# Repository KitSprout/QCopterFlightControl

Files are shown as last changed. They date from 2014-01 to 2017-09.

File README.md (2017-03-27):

QCopterFC
========





QCopterFC 是一個基於 STM32F4 的飛行控制器，主要用來實現濾波、平衡、控制等演算法的平台。集成微控制器 9 DOF 慣性測量元件以及氣壓計，目前有 QCopterFC 與 QCopterFCs 兩種版本，前者使用芯片效能較高、功能多、硬體完善，後者功能較為簡潔，以擴充方式實現不同需求，靈活度高。目前開發著重於 QCopterFCs，想了解 QCopterFC 的可以進入該分支 [branche](https://github.com/KitSprout/QCopterFlightControl/tree/QCopterFC)

Hardware
========
* 控制器　 : [STM32F411CE](http://www.st.com/en/microcontrollers/stm32f411ce.html) 48Pin 100MHz DSP FPU
* 感測器　 : [MPU9250](https://www.invensense.com/products/motion-tracking/9-axis/mpu-9250/) + [LPS22HB](http://www.st.com/en/mems-and-sensors/lps22hb.html)
* PCB 尺寸 : 26 * 26mm ( Screws M3: 20 * 20mm )
* 設計軟體 [Altium Designer 17](http://www.altium.com/en/products/altium-designer) ( PcbLib use AD [PcbLib v2.16](https://github.com/KitSprout/AltiumDesigner_PcbLibrary/releases/tag/v2.16) )

View
========


<br />
[more photo](https://goo.gl/photos/LVRgoCt4GyYr4dVZ8)...

Config
========


Schematic
========


Get it
========
Ruten Shop

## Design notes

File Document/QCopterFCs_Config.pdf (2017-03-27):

PORT | AF0 SYS | AF1 TIM1 TIM2 | AF2 TIM3 TIM4 TIM5 | AF3 TIM9 TIM10 TIM11 | AF4 I2C1 I2C2 I2C3 | AF5 SPI1 SPI2 SPI4 | AF6 SPI3 SPI4 SPI5 | AF7 SPI3 USART1 USART2 | AF8 USART6 | AF9 I2C2 I2C3 | AF10 OTG_FS | AF12 SDIO | ADC | 配置

PA

PB

PC

0 | CH1 / ETR | CH1 | CTS | ADC1_IN0 | O | EA0
1 | CH2 | CH2 | MOSI | RTS | ADC1_IN1 | O | EA1
2 | CH3 | CH3 | CH1 | TX | ADC1_IN2 | O | EA2
3 | CH4 | CH4 | CH2 | RX | ADC1_IN3 | O | EA3
4 | NSS | NSS | CK | ADC1_IN4 | O | IMU_CSM
5 | CH1 / ETR | SCK | ADC1_IN5 | O | IMU_SCK
6 | BKIN | CH1 | MISO | CMD | ADC1_IN6 | O | IMU_SDO
7 | CH1N | CH2 | MOSI | ADC1_IN7 | O | IMU_SDI
8 | MCO1 | CH1 | SCL | CK | SOF | D1 | O | EA8
9 | CH2 | SMBA | TX | VBUS | D2 | O | EA9
10 | CH3 | MOSI | RX | ID | O | EA10
11 | CH4 | MISO | CTS | TX | DM | X | USB_DM
12 | ETR | MISO | RTS | RX | DP | X | USB_DP
13 | SDIO | O | SWDIO
14 | SCLK | O | SWCLK
15 | JTDI | CH1 / ETR | NSS | NSS | TX | O | EA15
0 | CH2N | CH3 | SCK | ADC1_IN8 | O | EB0
1 | CH3N | CH4 | NSS | ADC1_IN9 | O | EB1
2 | BOOT | O | KEY
3 | JTDO | CH2 | SCK | SCK | RX | SDA | O | EB3
4 | JTRST | CH1 | MISO | MISO | SDA | D0 | O | EB4
5 | CH2 | SMBA | MOSI | MOSI | D3 | O | EB5
6 | CH1 | SCL | TX | O | EB6
7 | CH2 | SDA | RX | D0 | O | EB7
8 | CH3 | CH1 | SCL | MOSI | SDA | D4 | O | EB8
9 | CH4 | CH1 | SDA | NSS | SDA | D5 | O | EB9
10 | CH3 | SCL | SCK | D7 | O | IMU_CSB
11 | CH4 | X
12 | BKIN | SMBA | NSS | NSS | SCK | O | EP12
13 | CH1N | SCK | SCK | O | EB13
14 | CH2N | MISO | D6 | O | EB14
15 | RTC | CH3N | MOSI | CK | O | EB15
13 | O | LED_R
14 | O | LED_G
15 | O | LED_B

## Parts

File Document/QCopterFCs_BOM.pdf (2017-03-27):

Comment | Description | Designator | Footprint | LibRef | Quantity | Value
Cap_0603 | Capacitor | C1, C2, C3, C4 | CAP_0603 | Cap_0603 | 4 | 1u, 0.1u, 0.1u, 22n
Cap_0402 | Capacitor | C5, C6, C7, C8, C9, C11, C12, C13, C14, C15, C16 | CAP_0402 | Cap_0402 | 11 | 0.1u, 0.1u, 0.1u, 0.1u, 0.1u, 10p, 10p, 10n, 0.1u, 0.1u, 0.1u
Cap_Tan_0805 | Capacitor | C10 | CAP_TAN_P0805 | Cap_Tan_0805 | 1 | 2.2u
LED_0603 | LED | D1 | LED_0603_YELLOW | LED_0603 | 1
LED_1616_RGB | LED | D2 | LED_1616_RGB | LED_1616_RGB | 1
HDR2x10_1.27 | Header | HDR1, HDR2 | HDR2X10_1.27_18 0S | HDR2x10_1.27 | 2
ButtonTACT | Button | KEY | ButtonTACT_3.5*3. 55_90 | ButtonTACT | 1
Res_0402 | Resistor | R1, R2, R3, R5, R6, R7, R8, R9, R10, R11, R12 | RES_0402 | Res_0402 | 11 | 1.5K, 22R, 22R, 10K, 10K, 680R, 1K, 220R, 10K, 4.7K, 4.7K
Res_0603 | Resistor | R4 | RES_0603 | Res_0603 | 1 | 1K
RT9193 | Power | U1 | SOT23-5 | RT9193 | 1
STM32F411C | MCU | U2 | QFN_P0.5_48 | STM32F4x1C | 1
MPU925x | Sensor Motion | U3 | QFN_P0.4_24 | MPU925x | 1
LPS22HB | Sensor Pressure | U4 | HCLGA-2x2_10 | LPS22HB | 1
USB_Micro | USB | USB | USB_Micro-AB | USB_Micro | 1
XTAL_2520_4P | Crystal Oscillator | XT | XT_2520_4 | XTAL_2520_4P | 1 | 16MHz

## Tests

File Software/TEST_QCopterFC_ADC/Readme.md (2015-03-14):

QCopterFC ADC Example
========
* Author  : [Hom](about.me/Hom)
* Update  : 2014/05/06

Description
========
QCopterFC ADC 的範例程式，連續讀取 ADC_I 和 ADC_V 資料，同時 LED_G 會一直閃爍。

Hardware
========
* LED  
PC13 - LED_B  
PC14 - LED_G  
PC15 - LED_R  

* KEY  
PB2  - KEY  

* ADC  
PC4  - ADC_I  
PC5  - ADC_V  

* UART  
PB6 - UART Tx  
PB7 - UART Rx  
> UARTx = USART1  
> BaudRate = 115200  
> ByteSize = 8  
> StopBits = 1  
> Parity = 'N'  
> HardwareFlowControl = None

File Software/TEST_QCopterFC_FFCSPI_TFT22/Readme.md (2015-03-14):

QCopterFC FFCSPI-TFT2.2 Example
========
* Author  : [Hom](http://about.me/home)
* Update  : 2014/06/10

Description
========
QCopterFC FFCSPI-TFT2.2 的範例程式，透過 FFCSPI 讀寫 2.2 吋螢幕，並顯示彩條。

Hardware
========
* LED  
PC13 - LED_B  
PC14 - LED_G  
PC15 - LED_R  

* KEY  
PB2  - KEY  

* FFCSPI - TFT2.2  
PA4 - TFT22_CST  
PA5 - TFT22_SCK  
PA6 - TFT22_SDO  
PA7 - TFT22_SDI  
PC0 - TFT22_RST  
PC1 - TFT22_DC  
> SPIx = SPI1  
> Dir = 2Lines_FullDuplex  
> Mode = Slave  
> CPOL = High  
> CPHA = 2Edge  
> FirstBit = MSB  
> DataSize = 8 bits  
> BaudRate = Prescaler_2

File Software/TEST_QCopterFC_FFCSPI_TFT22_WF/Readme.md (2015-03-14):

QCopterFC FFCSPI-TFT2.2_WaveForm Example
========
* Author  : [Hom](http://about.me/home)
* Update  : 2014/06/10

Description
========
QCopterFC TFT2.2_WaveForm 的範例程式，透過 FFCSPI 讀寫 2.2 吋螢幕，計算三角函數並將波形顯示出來。

Hardware
========
* LED  
PC13 - LED_B  
PC14 - LED_G  
PC15 - LED_R  

* KEY  
PB2  - KEY  

* FFCSPI - TFT2.2  
PA4 - TFT22_CST  
PA5 - TFT22_SCK  
PA6 - TFT22_SDO  
PA7 - TFT22_SDI  
PC0 - TFT22_RST  
PC1 - TFT22_DC  
> SPIx = SPI1  
> Dir = 2Lines_FullDuplex  
> Mode = Slave  
> CPOL = High  
> CPHA = 2Edge  
> FirstBit = MSB  
> DataSize = 8 bits  
> BaudRate = Prescaler_2

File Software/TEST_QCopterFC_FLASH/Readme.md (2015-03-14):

QCopterFC FLASH Example
========
* Author  : [Hom](http://about.me/Hom)
* Update  : 2014/07/10

Description
========
QCopterFC FLASH 的範例程式，分成三種資料型態 U8 U16 U32 寫入，並讀出來比較是否正確，若正確則 LED 會依序發亮，最後一起閃爍。

Hardware
========
* LED  
PC13 - LED_B  
PC14 - LED_G  
PC15 - LED_R

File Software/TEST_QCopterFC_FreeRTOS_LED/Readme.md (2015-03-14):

QCopterFC LED Example
========
* Author  : [Hom](about.me/Hom)
* Update  : 2014/07/01

Description
========
QCopterFC 運行 FreeRTOS 的 LED 範例程式，LED_R 閃爍週期 1000 ms、LED_G 閃爍週期 500 ms、LED_B 閃爍週期 250 ms。  

Hardware
========
* LED  
PC13 - LED_B  
PC14 - LED_G  
PC15 - LED_R

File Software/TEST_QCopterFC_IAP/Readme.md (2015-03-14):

QCopterFC IAP Example
========
* Author  : [Hom](http://about.me/Hom)
* Update  : 2014/07/08

Description
========
QCopterFC IAP 的範例程式，按著 KEY 開機，將進入 BOOT 模式，此時會從 UART 接收 .bin 檔案，寫入至 APP FLASH 區域並執行，若開機未按下 KEY 則直接進入 APP 模式，執行最後更新的 APP 程式。  

Hardware
========
* LED  
PC13 - LED_B  
PC14 - LED_G  
PC15 - LED_R  

* KEY  
PB2  - KEY  

* UART  
PB6 - UART Tx  
PB7 - UART Rx  
> UARTx = USART1  
> BaudRate = 115200  
> ByteSize = 8  
> StopBits = 1  
> Parity = 'N'  
> HardwareFlowControl = None

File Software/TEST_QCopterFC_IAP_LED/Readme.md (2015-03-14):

QCopterFC IAP-LED Example
========
* Author  : [Hom](http://about.me/Hom)
* Update  : 2014/07/08

Description
========
QCopterFC IAP 的 LED 和 KEY 範例程式，啟動時 LED 會依序閃爍 ( R → G → B )，當按下按鍵 KEY 時，LED 則會同時閃爍，放開按鍵又會依序閃爍。  
 > 詳細參考 TEST_QCopterFC_LED

Hardware
========
* LED  
PC13 - LED_B  
PC14 - LED_G  
PC15 - LED_R  

* KEY  
PB2  - KEY

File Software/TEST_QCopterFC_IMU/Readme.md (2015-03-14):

QCopterFC IMU Example
========
* Author  : [Hom](http://about.me/Hom)
* Update  : 2014/06/10

Description
========
QCopterFC IMU 的範例程式，以 500Hz 讀取感測器，並透過 RS232 將資料傳送至 PC 端的 VisualScope 做顯示。

Hardware
========
* LED  
PC13 - LED_B  
PC14 - LED_G  
PC15 - LED_R  

* KEY  
PB2  - KEY  

* UART  
PB10 - UART Tx  
PB11 - UART Rx  
> UARTx = USART3  
> BaudRate = 9600  
> ByteSize = 8  
> StopBits = 1  
> Parity = 'N'  
> HardwareFlowControl = None  

* SPI  
PB13 - SPI_SCK  
PB14 - SPI_SDO  
PB15 - SPI_SDI  
PC2  - SPI_CSM  
> SPIx = SPI2  
> Dir = 2Lines_FullDuplex  
> Mode = Slave  
> CPOL = High  
> CPHA = 2Edge  
> FirstBit = MSB  
> DataSize = 8 bits  
> BaudRate = Prescaler_256

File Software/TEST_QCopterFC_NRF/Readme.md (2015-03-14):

QCopterFC NRF Example
========
* Author  : [Hom](about.me/Hom)
* Update  : 2014/05/12

Description
========
QCopterFC NRF 的範例程式，透過定義 NRF_MODE 來決定先發射還是先接收，
先發送的為 FTLR，先接收的為 FRLT，FTLR 板子會先傳送資料至 FRLT，
FRLT 收到後會直接回傳，並將資料透過 RS232 在 PC 端顯示，同時閃爍 LED_G & LED_B，
FTLR 則會將接收到的資料加上資料地址的數值發送至 FRLT，不斷循環，並閃爍 LED_R & LED_B。

Hardware
========
* LED  
PC13 - LED_B  
PC14 - LED_G  
PC15 - LED_R  

* KEY  
PB2  - KEY  

* UART  
PB6 - UART Tx  
PB7 - UART Rx  
> UARTx = USART1  
> BaudRate = 115200  
> ByteSize = 8  
> StopBits = 1  
> Parity = 'N'  
> HardwareFlowControl = None  

* NRF  
PA8  - CE  
PA15 - CSN  
PB3  - SCK  
PB4  - MISO  
PB5  - MOSI  
PB12 - IRQ  
> SPIx　　 = SPI3  
> Dir　　　= 2Lines_FullDuplex  
> Mode　　 = Master  
> CPOL　　 = Low  
> CPHA　　 = 1Edge  
> FirstBit = MSB  
> DataSize = 8 bits  
> BaudRate = Prescaler_4

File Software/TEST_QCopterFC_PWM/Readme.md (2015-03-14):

QCopterFC PWM Example
========
* Author  : [Hom](about.me/Hom)
* Update  : 2014/05/06

Description
========
QCopterFC PWM 的範例程式，按下按鍵 KEY 時，會改變 PWM 的 Duty Cycle，LED 同時會閃爍。

Hardware
========
* LED  
PC13 - LED_B  
PC14 - LED_G  
PC15 - LED_R  

* KEY  
PB2  - KEY  

* PWM  
PA0  - TIM2 CH1 - PWM1  
PA1  - TIM2 CH2 - PWM2  
PA2  - TIM2 CH3 - PWM3  
PA3  - TIM2 CH4 - PWM6  
PB0  - TIM3 CH3 - PWM5 
PB1  - TIM3 CH4 - PWM4  
PB8  - TIM4 CH3 - PWM10  
PB9  - TIM4 CH4 - PWM11  
PC6  - TIM3 CH1 - PWM8  
PC7  - TIM3 CH2 - PWM7

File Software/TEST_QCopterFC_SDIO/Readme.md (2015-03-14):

QCopterFC SDIO Example
========
* Author  : [Hom](about.me/Hom)
* Update  : 2014/05/09

Description
========
QCopterFC SDIO 搭配 FatFs 的範例程式，從一開始的 SD 卡初始化、SD 卡資訊、讀取資料夾目錄、寫檔案、讀檔案的整體測試。

Hardware
========
* LED  
PC13 - LED_B  
PC14 - LED_G  
PC15 - LED_R  

* UART  
PB6 - UART Tx  
PB7 - UART Rx  
> UARTx = USART1  
> BaudRate = 115200  
> ByteSize = 8  
> StopBits = 1  
> Parity = 'N'  
> HardwareFlowControl = None  

* SDIO  
PD8  - SDIO D0  
PD9  - SDIO D1  
PD10 - SDIO D2  
PD11 - SDIO D3  
PD12 - SDIO CK  
PD2  - SDIO CMD

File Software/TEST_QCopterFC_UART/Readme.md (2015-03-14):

QCopterFC UART Example
========
* Author  : [Hom](http://about.me/Hom)
* Update  : 2014/07/10

Description
========
QCopterFC UART 的範例程式，
USE_RS232：將鍵盤輸入的資料顯示在 Putty 上，同時綠色 LED 也會翻轉，
USE_VISUALSCOPE：將變數 i 透過 RS232 傳輸至電腦端，每傳一次 i 值就會加 1000，加到 32767 會從 -32768 重新開始再加，同時綠色 LED 也會閃爍。

Hardware
========
* LED  
PC13 - LED_B  
PC14 - LED_G  
PC15 - LED_R  

* UART  
PB6 - UART Tx  
PB7 - UART Rx  
> UARTx = USART1  
> BaudRate = 9600  
> ByteSize = 8  
> StopBits = 1  
> Parity = 'N'  
> HardwareFlowControl = None

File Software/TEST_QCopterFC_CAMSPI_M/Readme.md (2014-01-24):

QCopterFC CamSPI Master Example
========
* Author : [Hom](https://github.com/Hom19910422)
* Update : 2014/01/24

Description
========
QCopterFC CamSPI Master 的範例程式，當按下按鍵 KEY 時，CamSPI 會送出指令，並且接收回應，若正確 LED 則會發亮，最後會一起閃爍。  

Hardware
========
* LED  
PC13 - LED_B  
PC14 - LED_G  
PC15 - LED_R  

* KEY  
PB2  - KEY  

* CamSPI  
PA15 - CamSPI_CS  
PB3  - CamSPI_SCK  
PB4  - CamSPI_MISO  
PB5  - CamSPI_MOSI  
> SPIx = SPI3  
> Dir = 2Lines_FullDuplex  
> Mode = Master  
> CPOL = Low  
> CPHA = 1Edge  
> FirstBit = MSB  
> DataSize = 8 bits  
> BaudRate = Prescaler_256

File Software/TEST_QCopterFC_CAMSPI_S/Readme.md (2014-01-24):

QCopterFC CamSPI Slave Example
========
* Author : [Hom](https://github.com/Hom19910422)
* Update : 2014/01/24

Description
========
QCopterFC CamSPI Slave 的範例程式，接收到指令會回傳對應資料。  

Hardware
========
* LED  
PC13 - LED_B  
PC14 - LED_G  
PC15 - LED_R  

* CamSPI  
PA15 - CamSPI_CS  
PB3  - CamSPI_SCK  
PB4  - CamSPI_MISO  
PB5  - CamSPI_MOSI  
> SPIx = SPI3  
> Dir = 2Lines_FullDuplex  
> Mode = Slave  
> CPOL = Low  
> CPHA = 1Edge  
> FirstBit = MSB  
> DataSize = 8 bits  
> BaudRate = Prescaler_256

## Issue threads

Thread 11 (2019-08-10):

關於MPU9250的加速度計問題

smallchicken0204, 2019-08-10:
您好，我是台北大學資工系的研究生，目前做的研究是將IMU放置在手腕上追蹤手部軌跡，而遇到的問題是，當加速度計從運動狀態急停的時候，似乎會出現與運動方向相反的加速度，導致軌跡會出現到達目標位置時(15CM處)，瞬間往後倒退3~5CM(12CM處)，想詢問您有沒有遇過相關的問題?

brennenhuang, 2019-08-10:
請問是real time還是事後分析呢？

smallchicken0204 <notifications@github.com>於 2019年8月10日 週六，下午5:02寫道：

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

smallchicken0204, 2019-08-10:
real time的，我是設計成每收集20筆加速度資料，進行一次計算。

brennenhuang, 2019-08-10:
如果軌跡在動時有明確的起始，那可以用零速補償，如果是一直持續的動態一定會有積分飄移，然後記得用濾波器濾雜訊

smallchicken0204 <notifications@github.com>於 2019年8月10日 週六，下午8:35寫道：

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

smallchicken0204, 2019-08-10:
瞭解，目前有使用簡易的零速補償，我先嘗試去改良一下零速補償這塊看看，感謝您的回答。

brennenhuang, 2019-08-11:
加油keep going

smallchicken0204 <notifications@github.com>於 2019年8月10日 週六，下午10:12寫道：

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

smallchicken0204, 2019-10-03:
您好，我想再跟您請教一下MPU9250的問題，目前我打算驗證位移距離，所以做了一個軌道平台(如附圖一)，這平台是讓IMU單純沿著x軸來回滑動且軌道算是光滑不會震動，但是發現row data裡面的Z軸加速度會出現過大的振幅，所以我做了一個測試是在軌道滑動數次，再用手持IMU在空中移動數次，得到row data(如附圖二)Y軸是加速度(單位:g)X軸為樣本數，左邊紅色框框是在軌道上滑動得到的數值，右邊紅色框框則是空中滑動的，因為差異其實蠻大的，我不太能確定是否全為摩擦震動導致，想詢問您有沒有遇過相關的情況?
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

Closed 2019-10-08.

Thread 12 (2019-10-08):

MPU9250加速度Z軸的問題

smallchicken0204, 2019-10-08:
您好，我想跟您請教一下MPU9250的問題，目前我打算驗證位移距離，所以做了一個軌道平台(如附圖一)，這平台是讓IMU單純沿著x軸來回滑動，而且軌道算是光滑不會震動，但是發現row data裡面的Z軸加速度會出現過大的振幅，所以我做了一個測試是在軌道滑動數次，再用手持IMU在空中移動數次，得到row data(如附圖二)Y軸是加速度(單位:g)X軸為樣本數，左邊紅色框框是在軌道上滑動得到的數值，右邊紅色框框則是空中滑動的，因為差異其實蠻大的，我不太能確定是否全為摩擦震動導致，想詢問您有沒有遇過相關的情況?
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

brennenhuang, 2019-10-09:
看起來Z軸呈現的確實怪,你要不要把他的Z軸跟X軸或Y軸對調,重複做一樣的實驗,看會不會重現此問題,讓x或y軸朝上,祝你一切順利

On Tue, Oct 8, 2019 at 4:41 PM smallchicken0204 <notifications@github.com>
wrote:

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

smallchicken0204, 2019-10-10:
對調Y軸跟Z軸後，意外發現問題所在了，謝謝您的建議~

brennenhuang, 2019-10-10:
讚喔，之後有問題也可以用賴問，研究的問題通常都不太能等，我的賴：jimpaul15，如果有要加可以說一聲，我剛好也在台北工作，加油嘍，對了也可以用email問，只是通常可能不會天天看email

smallchicken0204 <notifications@github.com>於 2019年10月10日 週四，下午3:42寫道：

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

smallchicken0204, 2019-10-11:
好的，那我加一下您的Line。

Closed 2019-10-10.

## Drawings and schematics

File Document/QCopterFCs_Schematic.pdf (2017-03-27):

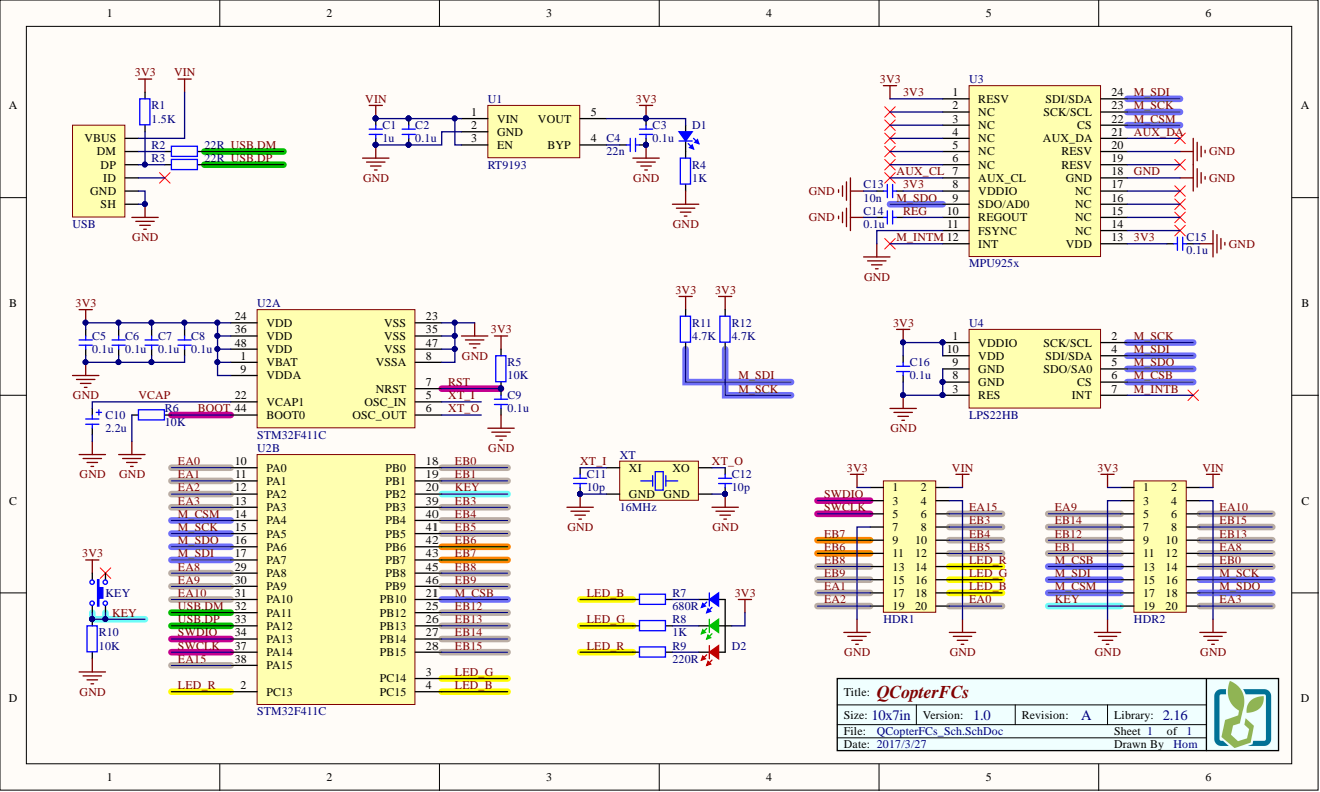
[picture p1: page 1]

3 6 | 3 5
4 8 | 4 7

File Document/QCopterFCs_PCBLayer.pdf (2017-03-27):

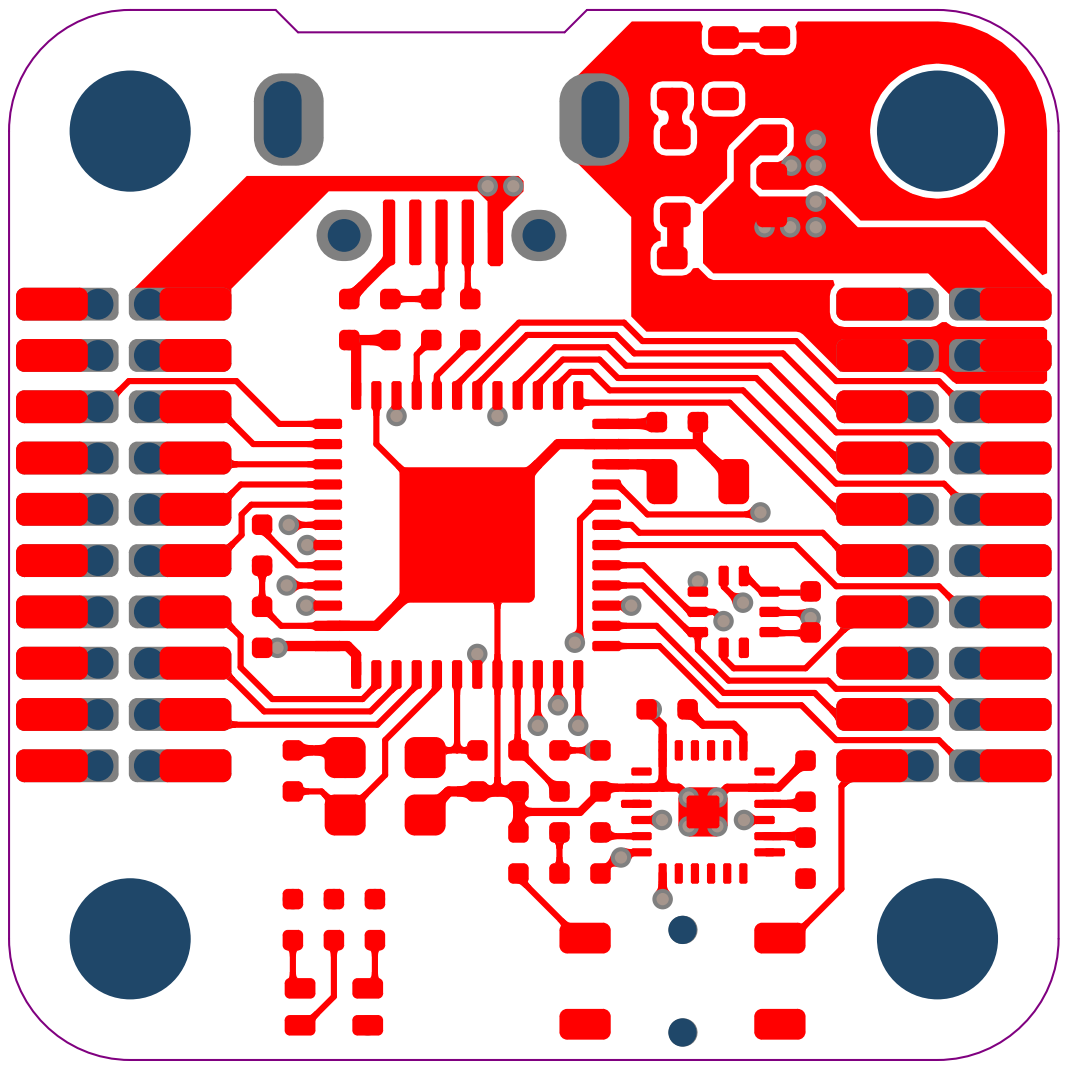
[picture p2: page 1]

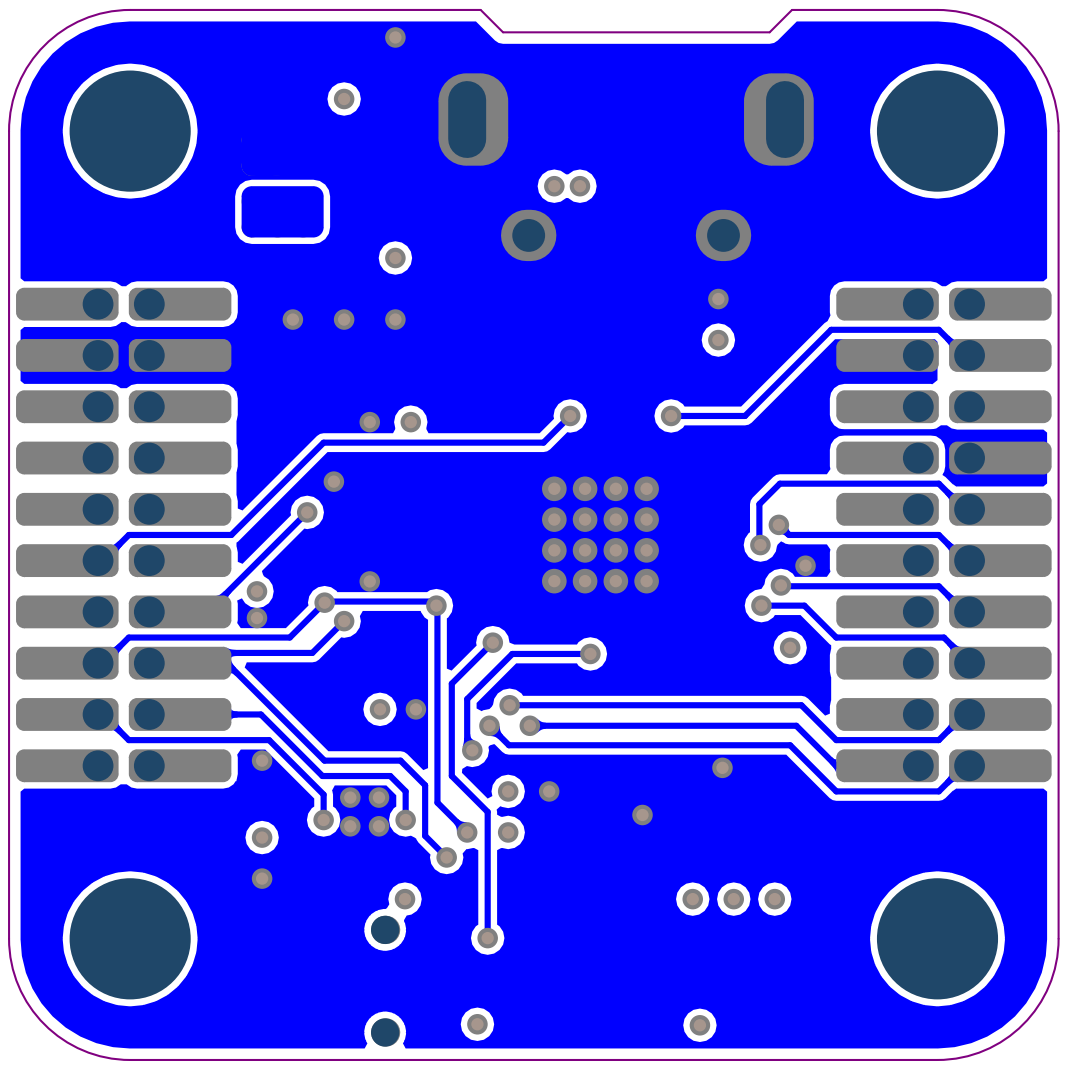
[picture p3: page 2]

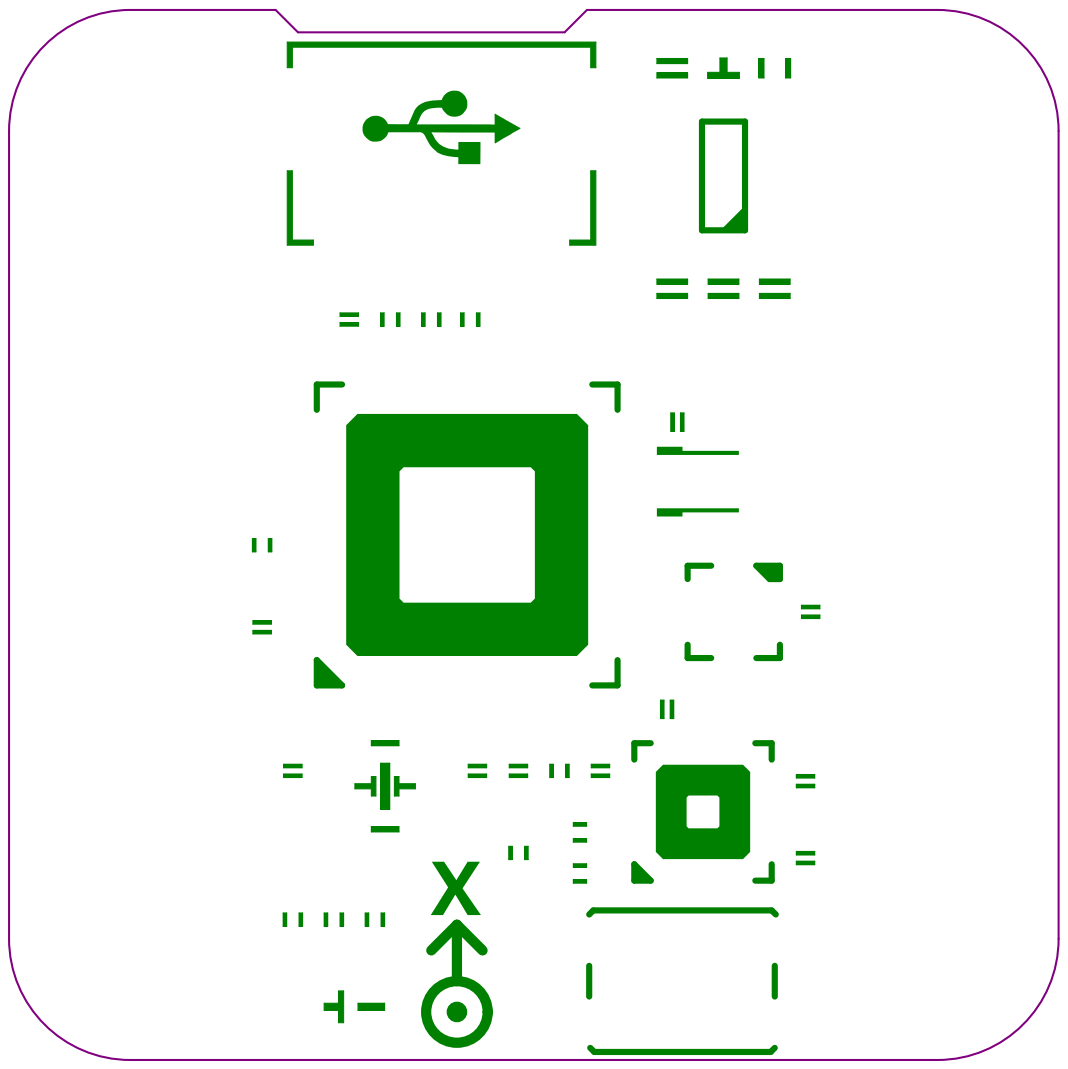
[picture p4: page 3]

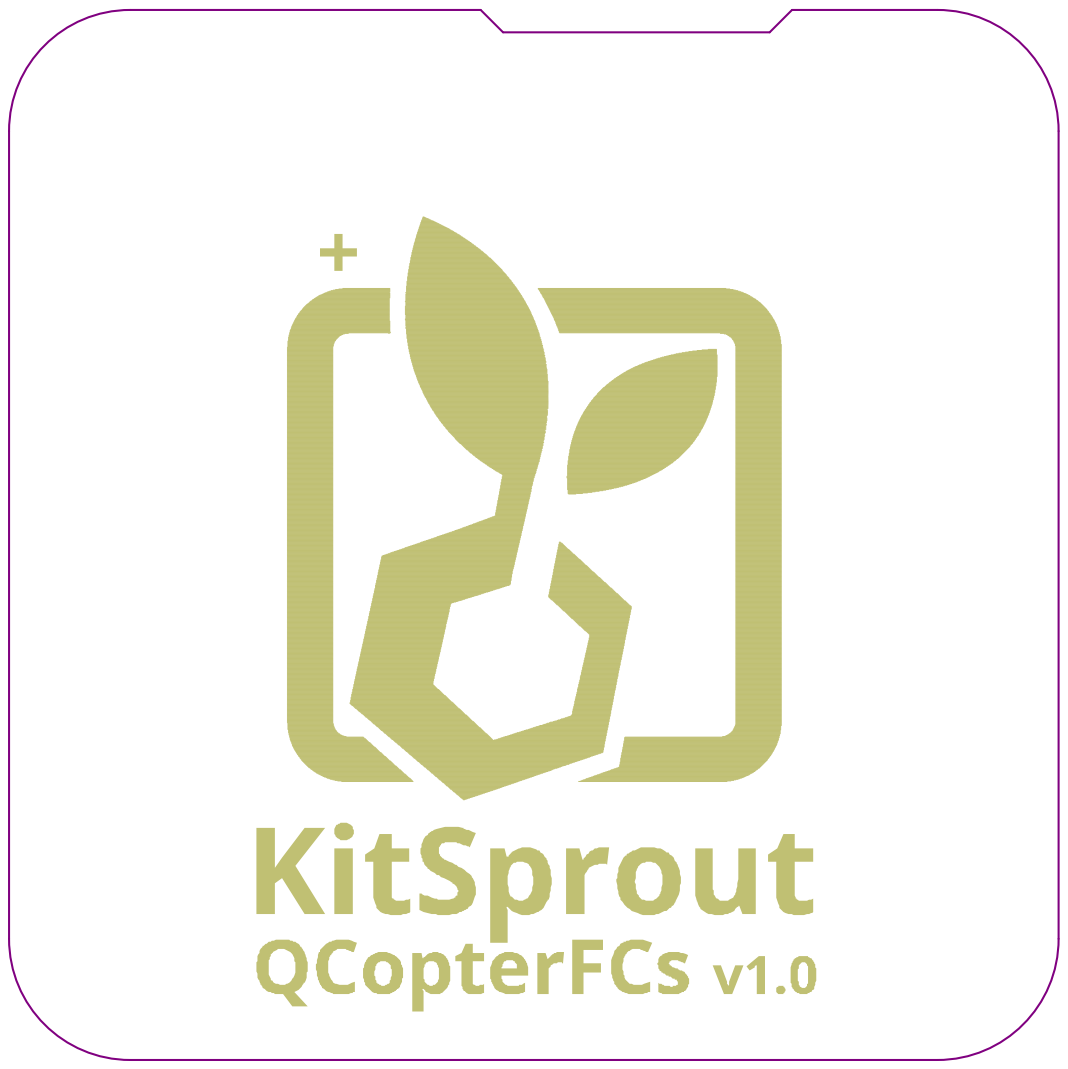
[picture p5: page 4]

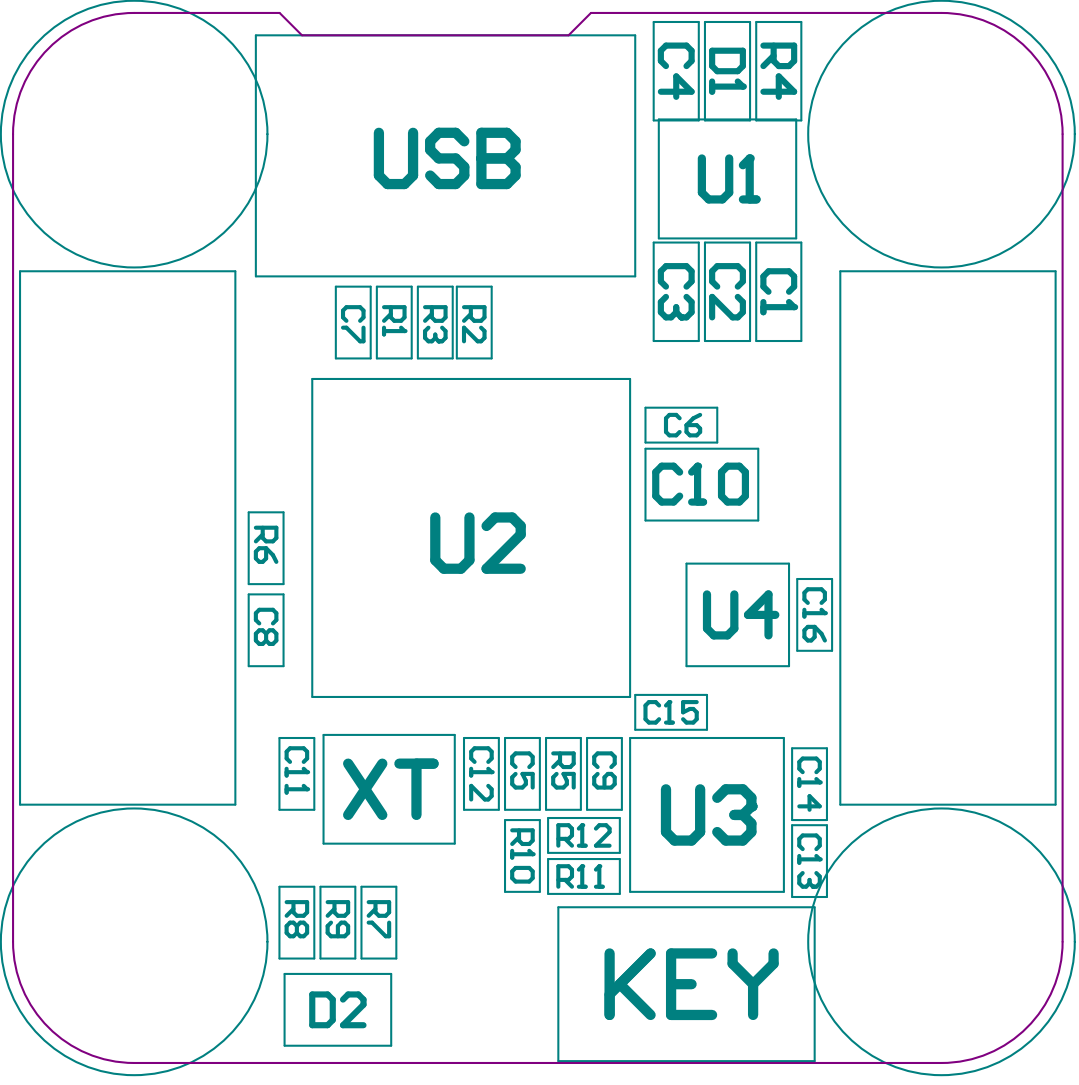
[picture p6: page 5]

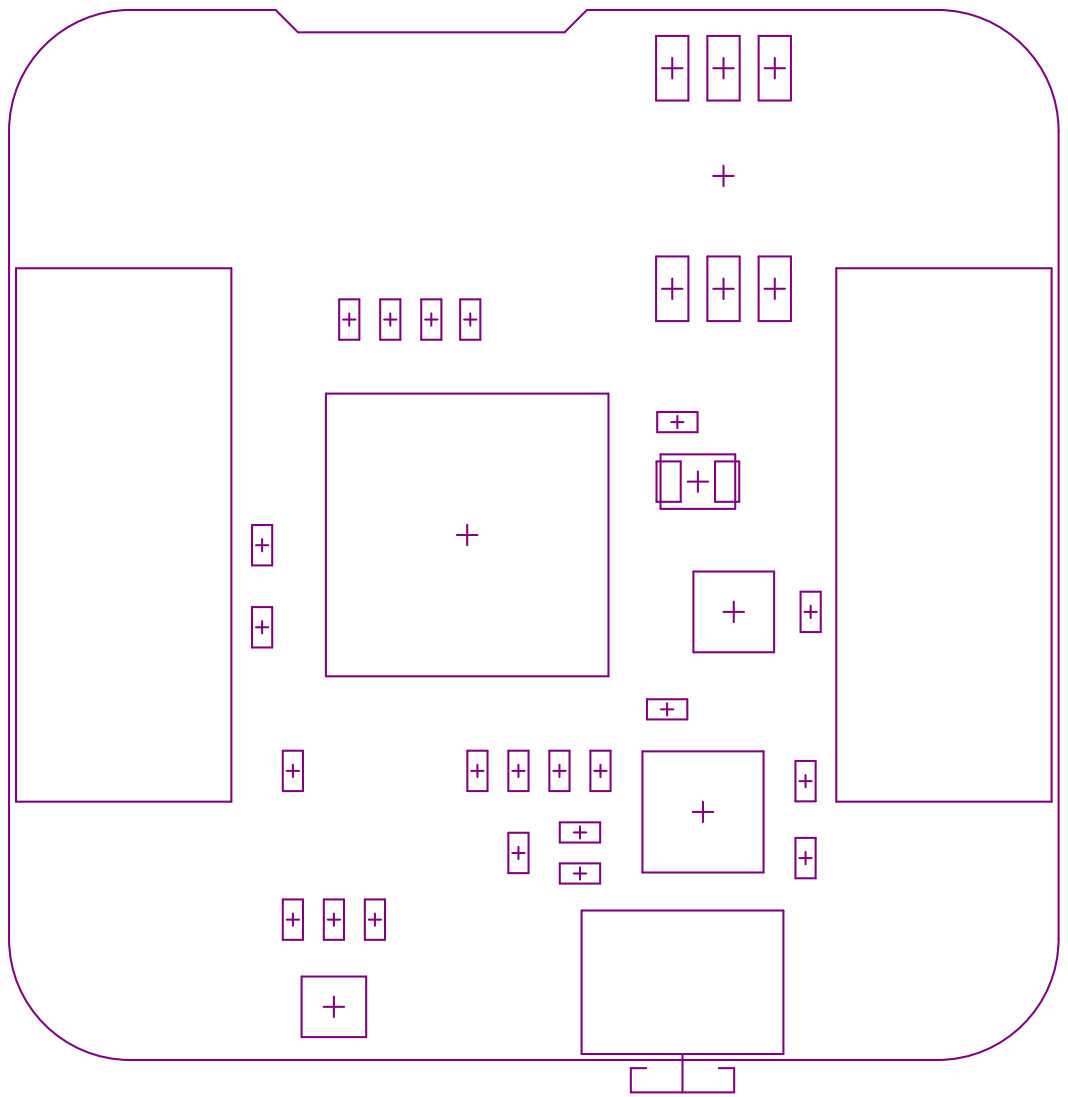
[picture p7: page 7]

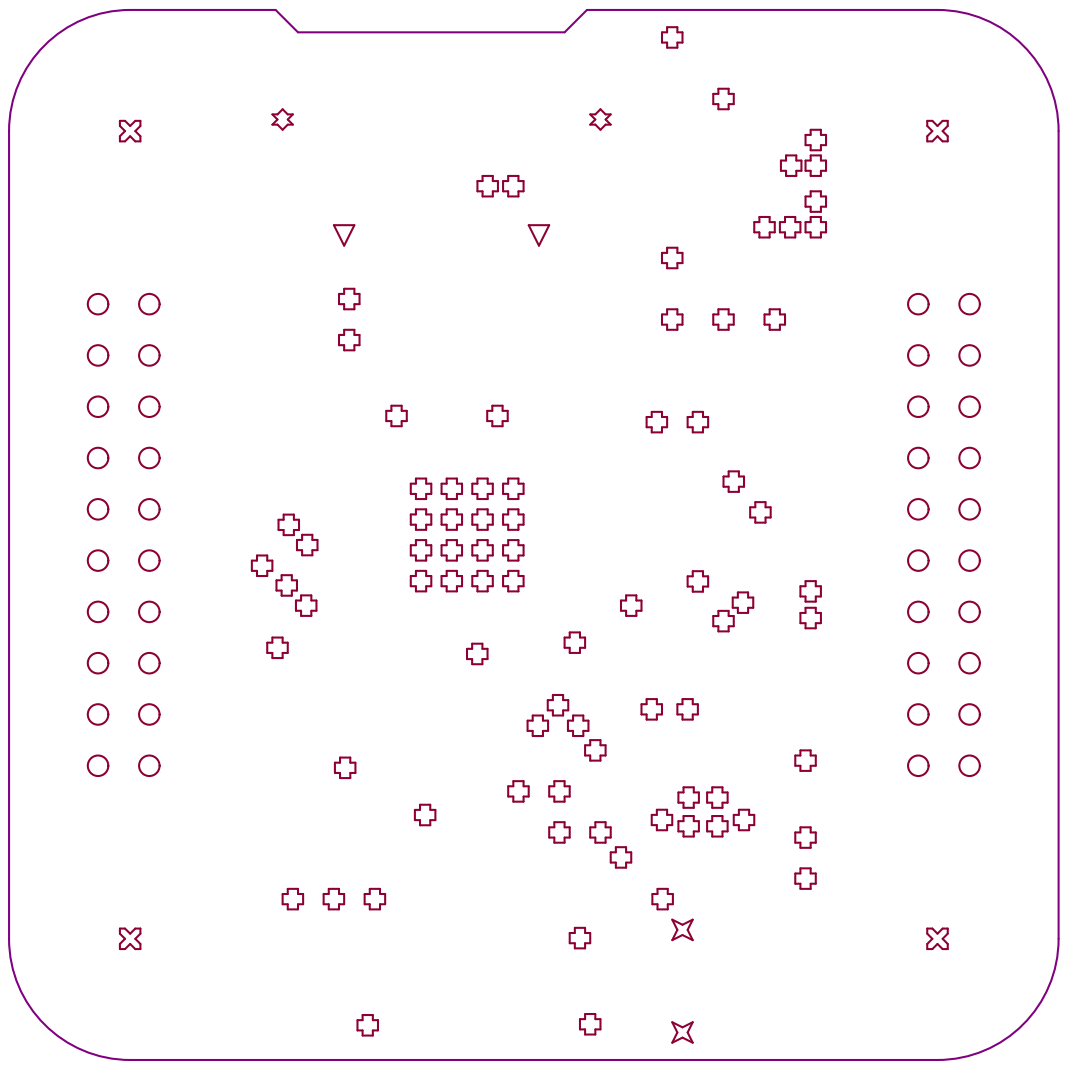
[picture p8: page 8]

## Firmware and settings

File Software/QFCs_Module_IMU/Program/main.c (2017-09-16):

/**
  *      __            ____
  *     / /__ _  __   / __/                      __  
  *    / //_/(_)/ /_ / /  ___   ____ ___  __ __ / /_ 
  *   / ,<  / // __/_\ \ / _ \ / __// _ \/ // // __/ 
  *  /_/|_|/_/ \__//___// .__//_/   \___/\_,_/ \__/  
  *                    /_/   github.com/KitSprout    
  * 
  * @file    main.c
  * @author  KitSprout
  * @date    16-Mar-2017
  * @brief   
  * 
  */

/* Includes --------------------------------------------------------------------------------*/
#include "drivers\stm32f4_system.h"
#include "modules\serial.h"
#include "modules\kSerial.h"
#include "modules\imu.h"
#include "stm32f4xx_bsp.h"

/** @addtogroup STM32_Program
  * @{
  */

/* Private typedef -------------------------------------------------------------------------*/
/* Private define --------------------------------------------------------------------------*/
#define PACKET_LENS 9

/* Private macro ---------------------------------------------------------------------------*/
/* Private variables -----------------------------------------------------------------------*/
extern IMU_DataTypeDef imu;
float32_t FIFO_P[16] = {0};

/* Private function prototypes -------------------------------------------------------------*/
/* Private functions -----------------------------------------------------------------------*/

int main( void )
{
  HAL_Init();
  BSP_GPIO_Config();
  BSP_UART_SERIAL_Config(NULL);
  BSP_SPI_IMU_Config();

  while (1) {

#if 0
    LED_B_Toggle();
    delay_ms(100);
    IMU_GetRealData(&imu);
    printf("GX:%5i\tGY:%5i\tGZ:%5i\tAX:%5i\tAY:%5i\tAZ:%5i\tMX:%5i\tMY:%5i\tMZ:%5i\r\n",
      imu.gyrRaw[0], imu.gyrRaw[1], imu.gyrRaw[2],
      imu.accRaw[0], imu.accRaw[1], imu.accRaw[2],
      imu.magRaw[0], imu.magRaw[1], imu.magRaw[2]
    );
#endif

#if 1
    LED_B_Toggle();
    delay_ms(100);
    IMU_GetRealData(&imu);

    float32_t tmp = 0;
    float32_t pressure, temperature, altitude;
    for (uint8_t i = 0; i < 15; i++) {
      FIFO_P[i] = FIFO_P[i + 1];
    }
    FIFO_P[15] = imu.baroData[0];

    for (uint8_t i = 0; i < 16; i++) {
      tmp += FIFO_P[i];
    }
    pressure    = tmp / 16.0f;
    temperature = imu.baroData[1];
    altitude    = (powf(1015.7f / pressure, 0.1902630958f) - 1.0f) * 45869.2308f;

    printf("[GYR]%8.2f, %8.2f, %8.2f [ACC]%7.4f, %7.4f, %7.4f [MAG]%6.1f, %6.1f, %6.1f [BAR] %8.2f, %7.2f, %8.2f\r\n",
      imu.gyrData[0], imu.gyrData[1], imu.gyrData[2],
      imu.accData[0], imu.accData[1], imu.accData[2],
      imu.magData[0], imu.magData[1], imu.magData[2],
      pressure, temperature, altitude
    );
#endif

#if 0
    int16_t sendBuf[PACKET_LENS];
    LED_B_Toggle();
    IMU_GetRealData(&imu);
    sendBuf[0] = imu.gyrRaw[0];
    sendBuf[1] = imu.gyrRaw[1];
    sendBuf[2] = imu.gyrRaw[2];
    sendBuf[3] = imu.accRaw[0];
    sendBuf[4] = imu.accRaw[1];
    sendBuf[5] = imu.accRaw[2];
    sendBuf[6] = imu.magRaw[0];
    sendBuf[7] = imu.magRaw[1];
    sendBuf[8] = imu.magRaw[2];
    kSerial_SendData(sendBuf, PACKET_LENS, KS_INT16);
#endif

  }
}

/*************************************** END OF FILE ****************************************/

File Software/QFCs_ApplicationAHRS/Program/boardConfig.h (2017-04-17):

/**
  *      __            ____
  *     / /__ _  __   / __/                      __  
  *    / //_/(_)/ /_ / /  ___   ____ ___  __ __ / /_ 
  *   / ,<  / // __/_\ \ / _ \ / __// _ \/ // // __/ 
  *  /_/|_|/_/ \__//___// .__//_/   \___/\_,_/ \__/  
  *                    /_/   github.com/KitSprout    
  * 
  * @file    boardConfig.h
  * @author  KitSprout
  * @date    16-Mar-2017
  * @brief   
  * 
  */

/* Define to prevent recursive inclusion ---------------------------------------------------*/
#ifndef __BOARDCONFIG_H
#define __BOARDCONFIG_H

#ifdef __cplusplus
 extern "C" {
#endif

/* Includes --------------------------------------------------------------------------------*/
/* Exported types --------------------------------------------------------------------------*/
/* Exported constants ----------------------------------------------------------------------*/

#define KS_HW_BOARD_NAME              "QCopterFCs"
#define KS_HW_MCU_NAME                "STM32F411CE"

#define KS_HW_CLOCK_SOUCE_HSE
//#define KS_HW_USE_CLOCK_SOUCE_HSI

//#define KS_HW_UART_HAL_LIBRARY
//#define KS_HW_SPI_HAL_LIBRARY


/* -------- LED and KEY */
   
#define LED_R_PIN                     GPIO_PIN_13
#define LED_R_GPIO_PORT               GPIOC
#define LED_R_Set()                   __GPIO_SET(LED_R_GPIO_PORT, LED_R_PIN)
#define LED_R_Reset()                 __GPIO_RST(LED_R_GPIO_PORT, LED_R_PIN)
#define LED_R_Toggle()                __GPIO_TOG(LED_R_GPIO_PORT, LED_R_PIN)

#define LED_G_PIN                     GPIO_PIN_14
#define LED_G_GPIO_PORT               GPIOC
#define LED_G_Set()                   __GPIO_SET(LED_G_GPIO_PORT, LED_G_PIN)
#define LED_G_Reset()                 __GPIO_RST(LED_G_GPIO_PORT, LED_G_PIN)
#define LED_G_Toggle()                __GPIO_TOG(LED_G_GPIO_PORT, LED_G_PIN)

#define LED_B_PIN                     GPIO_PIN_15
#define LED_B_GPIO_PORT               GPIOC
#define LED_B_Set()                   __GPIO_SET(LED_B_GPIO_PORT, LED_B_PIN)
#define LED_B_Reset()                 __GPIO_RST(LED_B_GPIO_PORT, LED_B_PIN)
#define LED_B_Toggle()                __GPIO_TOG(LED_B_GPIO_PORT, LED_B_PIN)

#define KEY_PIN                       GPIO_PIN_2
#define KEY_GPIO_PORT                 GPIOB
#define KEY_Read()                    (__GPIO_READ(KEY_GPIO_PORT, KEY_PIN) == KEY_PIN)


/* -------- TIM Timer */

#define AHRS_TIMx                     TIM3
#define AHRS_TIMx_CLK_ENABLE()        __HAL_RCC_TIM3_CLK_ENABLE()
#define AHRS_TIMx_IRQn                TIM3_IRQn
#define AHRS_TIMx_IRQn_PREEMPT        0x0F
#define AHRS_TIMx_IRQn_SUB            1

#define __SAMPLE_RATE_1KHz_

#ifdef __SAMPLE_RATE_100Hz_
  #define SAMPLE_RATE   ((uint16_t)100)       // 100Hz
  #define SAMPLE_TIME   ((float32_t)0.01f)    // 10ms
#endif

#ifdef __SAMPLE_RATE_200Hz_
  #define SAMPLE_RATE   ((uint16_t)200)       // 200Hz
  #define SAMPLE_TIME   ((float32_t)0.005f)   // 5ms
#endif

#ifdef __SAMPLE_RATE_400Hz_
  #define SAMPLE_RATE   ((uint16_t)400)       // 400Hz
  #define SAMPLE_TIME   ((float32_t)0.0025f)  // 2.5ms
#endif

#ifdef __SAMPLE_RATE_500Hz_
  #define SAMPLE_RATE   ((uint16_t)500)       // 500Hz
  #define SAMPLE_TIME   ((float32_t)0.002f)   // 2.0ms
#endif

#ifdef __SAMPLE_RATE_1KHz_
  #define SAMPLE_RATE   ((uint16_t)1000)      // 1KHz
  #define SAMPLE_TIME   ((float32_t)0.001f)   // 1.0ms
#endif


/* -------- UART Serial */

#define SERIAL_MAX_TXBUF              16
#define SERIAL_MAX_RXBUF              16

#define SERIAL_UARTx                  USART1
#define SERIAL_UARTx_CLK_ENABLE()     __HAL_RCC_USART1_CLK_ENABLE()
#define SERIAL_UARTx_IRQn             USART1_IRQn
#define SERIAL_UARTx_IRQn_PREEMPT     0x0F
#define SERIAL_UARTx_IRQn_SUB         1

#define SERIAL_UARTx_FORCE_RESET()    __HAL_RCC_USART1_FORCE_RESET()
#define SERIAL_UARTx_RELEASE_RESET()  __HAL_RCC_USART1_RELEASE_RESET()

#define SERIAL_TX_PIN                 GPIO_PIN_6
#define SERIAL_TX_GPIO_PORT           GPIOB
#define SERIAL_TX_AF                  GPIO_AF7_USART1

#define SERIAL_RX_PIN                 GPIO_PIN_7
#define SERIAL_RX_GPIO_PORT           GPIOB
#define SERIAL_RX_AF                  GPIO_AF7_USART1

#define SERIAL_BAUDRATE               115200
#define SERIAL_BYTESIZE               UART_WORDLENGTH_8B
#define SERIAL_STOPBITS               UART_STOPBITS_1
#define SERIAL_PARITY                 UART_PARITY_NONE
#define SERIAL_HARDWARECTRL           UART_HWCONTROL_NONE
#define SERIAL_MODE                   UART_MODE_TX_RX
#define SERIAL_OVERSAMPLE             UART_OVERSAMPLING_16


/* -------- Inertial Sensor */

#define IMU_MAX_TXBUF                 32
#define IMU_MAX_RXBUF                 32
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

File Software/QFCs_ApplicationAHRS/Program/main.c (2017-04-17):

/**
  *      __            ____
  *     / /__ _  __   / __/                      __  
  *    / //_/(_)/ /_ / /  ___   ____ ___  __ __ / /_ 
  *   / ,<  / // __/_\ \ / _ \ / __// _ \/ // // __/ 
  *  /_/|_|/_/ \__//___// .__//_/   \___/\_,_/ \__/  
  *                    /_/   github.com/KitSprout    
  * 
  * @file    main.c
  * @author  KitSprout
  * @date    16-Mar-2017
  * @brief   
  * 
  */

/* Includes --------------------------------------------------------------------------------*/
#include "drivers\stm32f4_system.h"
#include "modules\serial.h"
#include "modules\kSerial.h"
#include "modules\imu.h"
#include "algorithms\ahrs.h"
#include "stm32f4xx_bsp.h"

/** @addtogroup STM32_Program
  * @{
  */

/* Private typedef -------------------------------------------------------------------------*/
/* Private define --------------------------------------------------------------------------*/
#define PACKET_LENS 15

/* Private macro ---------------------------------------------------------------------------*/
/* Private variables -----------------------------------------------------------------------*/
ahrs_t ahrs;

static uint16_t sec = 0;
static uint16_t msec = 0;
static int16_t sendBuf[PACKET_LENS] = {0};

__IO static uint8_t flag = ERROR;

/* Private function prototypes -------------------------------------------------------------*/
void IRQEvent_AHRS( void );

/* Private functions -----------------------------------------------------------------------*/

int main( void )
{
  HAL_Init();
  BSP_GPIO_Config();
  BSP_UART_SERIAL_Config(NULL);
  BSP_SPI_IMU_Config();
  BSP_AHRS_Config(IRQEvent_AHRS, SAMPLE_RATE);

  while (1) {

#if 0
    LED_B_Toggle();
    delay_ms(100);
#if 0
    printf("GX:%5i\tGY:%5i\tGZ:%5i\tAX:%5i\tAY:%5i\tAZ:%5i\tMX:%6.1f\tMY:%6.1f\tMZ:%6.1f\r\n",
      ahrs.imu.gyrInt[0], ahrs.imu.gyrInt[1], ahrs.imu.gyrInt[2],
      ahrs.imu.accInt[0], ahrs.imu.accInt[1], ahrs.imu.accInt[2],
      ahrs.imu.magInt[0], ahrs.imu.magInt[1], ahrs.imu.magInt[2]
    );
#else
    printf("GX:%8.2f\tGY:%8.2f\tGZ:%5.2f\tAX:%7.4f\tAY:%7.4f\tAZ:%7.4f\tMX:%6.1f\tMY:%6.1f\tMZ:%6.1f\r\n",
      ahrs.imu.gyrData[0], ahrs.imu.gyrData[1], ahrs.imu.gyrData[2],
      ahrs.imu.accData[0], ahrs.imu.accData[1], ahrs.imu.accData[2],
//      ahrs.imu.magData[0], ahrs.imu.magData[1], ahrs.imu.magData[2]
      ahrs.angE.pitch, ahrs.angE.roll, ahrs.angE.yaw
    );
#endif

#else
    LED_G_Toggle();
    if (flag == ENABLE) {
      flag = DISABLE;
      sendBuf[0]  = ahrs.imu.gyrInt[0];
      sendBuf[1]  = ahrs.imu.gyrInt[1];
      sendBuf[2]  = ahrs.imu.gyrInt[2];
      sendBuf[3]  = ahrs.imu.accInt[0];
      sendBuf[4]  = ahrs.imu.accInt[1];
      sendBuf[5]  = ahrs.imu.accInt[2];
      sendBuf[6]  = ahrs.imu.magInt[0];
      sendBuf[7]  = ahrs.imu.magInt[1];
      sendBuf[8]  = ahrs.imu.magInt[2];
      sendBuf[9]  = ahrs.numQ.q0 * 10000;
      sendBuf[10] = ahrs.numQ.q1 * 10000;
      sendBuf[11] = ahrs.numQ.q2 * 10000;
      sendBuf[12] = ahrs.numQ.q3 * 10000;
      sendBuf[13] = sec;
      sendBuf[14] = msec;
      kSerial_SendData(sendBuf, PACKET_LENS, KS_INT16);
    }
#endif
  }
}

void IRQEvent_AHRS( void )
{
  if (++msec >= SAMPLE_RATE) {
    msec = 0;
    sec++;
  }

  IMU_GetRealData(&ahrs.imu);
  AHRS_GyroBiasCorrection(ahrs.imu.gyrRaw, ahrs.imu.gyrOffset);
  AHRS_Update(&ahrs);
  flag = ENABLE;
}

/*************************************** END OF FILE ****************************************/

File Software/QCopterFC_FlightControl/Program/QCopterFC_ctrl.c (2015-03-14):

/*=====================================================================================================*/
/*=====================================================================================================*/
#include "stm32f4_system.h"
#include "QCopterFC_board.h"
#include "QCopterFC_ctrl.h"
#include "QCopterFC_transport.h"
/*=====================================================================================================*/
/*=====================================================================================================*/
vu16 BasicThr = 0;  // 0 ~ 10000 對應到 0.00% ~ 100.00%
/*=====================================================================================================*/
/*=====================================================================================================*
**函數 : BLDC_Config
**功能 : 設定PWM輸出訊號
**輸入 : None
**輸出 : None
**使用 : BLDC_Config();
**=====================================================================================================*/
/*=====================================================================================================*/
void BLDC_Config( void )
{
  GPIO_InitTypeDef GPIO_InitStruct;
  TIM_TimeBaseInitTypeDef TIM_TimeBaseStruct;
  TIM_OCInitTypeDef TIM_OCInitStruct;

  /* TIM Clk Init *************************************************************/
  RCC_AHB1PeriphClockCmd(RCC_AHB1Periph_GPIOA | RCC_AHB1Periph_GPIOB | RCC_AHB1Periph_GPIOC, ENABLE);
  RCC_APB1PeriphClockCmd(RCC_APB1Periph_TIM2 | RCC_APB1Periph_TIM3 | RCC_APB1Periph_TIM4, ENABLE);

  GPIO_PinAFConfig(GPIOA, GPIO_PinSource0, GPIO_AF_TIM2);
  GPIO_PinAFConfig(GPIOA, GPIO_PinSource1, GPIO_AF_TIM2);
  GPIO_PinAFConfig(GPIOA, GPIO_PinSource2, GPIO_AF_TIM2);
  GPIO_PinAFConfig(GPIOA, GPIO_PinSource3, GPIO_AF_TIM2);
  GPIO_PinAFConfig(GPIOB, GPIO_PinSource0, GPIO_AF_TIM3);
  GPIO_PinAFConfig(GPIOB, GPIO_PinSource1, GPIO_AF_TIM3);
  GPIO_PinAFConfig(GPIOB, GPIO_PinSource8, GPIO_AF_TIM4);
  GPIO_PinAFConfig(GPIOB, GPIO_PinSource9, GPIO_AF_TIM4);
  GPIO_PinAFConfig(GPIOC, GPIO_PinSource6, GPIO_AF_TIM3);
  GPIO_PinAFConfig(GPIOC, GPIO_PinSource7, GPIO_AF_TIM3);

  /* TIM2 PWM1 PA0  */ /* TIM2 PWM2 PA1  */ /* TIM2 PWM3 PA2  */ /* TIM2 PWM6 PA3 */
  GPIO_InitStruct.GPIO_Pin = GPIO_Pin_0 | GPIO_Pin_1 | GPIO_Pin_2 | GPIO_Pin_3 | GPIO_Pin_6 | GPIO_Pin_7;
  GPIO_InitStruct.GPIO_Mode = GPIO_Mode_AF;
  GPIO_InitStruct.GPIO_Speed = GPIO_Speed_100MHz;
  GPIO_InitStruct.GPIO_OType = GPIO_OType_PP;
  GPIO_InitStruct.GPIO_PuPd = GPIO_PuPd_UP;
  GPIO_Init(GPIOA, &GPIO_InitStruct);
  /* TIM3 PWM5 PB0  */ /* TIM3 PWM4 PB1  */ /* TIM4 PWM10 PB8 */ /* TIM4 PWM11 PB9 */
  GPIO_InitStruct.GPIO_Pin = GPIO_Pin_0 | GPIO_Pin_1 | GPIO_Pin_8 | GPIO_Pin_9;
  GPIO_InitStruct.GPIO_Mode = GPIO_Mode_AF;
  GPIO_InitStruct.GPIO_Speed = GPIO_Speed_100MHz;
  GPIO_InitStruct.GPIO_OType = GPIO_OType_PP;
  GPIO_InitStruct.GPIO_PuPd = GPIO_PuPd_UP;
  GPIO_Init(GPIOB, &GPIO_InitStruct);
  /* TIM3 PWM8 PC6  */ /* TIM3 PWM7 PC7 */
  GPIO_InitStruct.GPIO_Pin = GPIO_Pin_6 | GPIO_Pin_7;
  GPIO_InitStruct.GPIO_Mode = GPIO_Mode_AF;
  GPIO_InitStruct.GPIO_Speed = GPIO_Speed_100MHz;
  GPIO_InitStruct.GPIO_OType = GPIO_OType_PP;
  GPIO_InitStruct.GPIO_PuPd = GPIO_PuPd_UP;
  GPIO_Init(GPIOC, &GPIO_InitStruct);

  TIM_DeInit(TIM2);
  TIM_DeInit(TIM3);
  TIM_DeInit(TIM4);

  /************************** PWM Output **************************************/
  /* TIM2 TIM3 TIM4 Time Base */
  TIM_TimeBaseStruct.TIM_Period = (u16)(2500-1);              // Period = 2.5ms => Freq = 400Hz
  TIM_TimeBaseStruct.TIM_Prescaler = (u16)(84-1);             // fCK_PSC / 84 = 1M ( 1us )
  TIM_TimeBaseStruct.TIM_ClockDivision = TIM_CKD_DIV1;
  TIM_TimeBaseStruct.TIM_CounterMode = TIM_CounterMode_Up;    // Count Up
  TIM_TimeBaseInit(TIM2, &TIM_TimeBaseStruct);
  TIM_TimeBaseInit(TIM3, &TIM_TimeBaseStruct);
  TIM_TimeBaseInit(TIM4, &TIM_TimeBaseStruct);

  /* TIM2 TIM3 TIM4 OC */
  TIM_OCInitStruct.TIM_OCMode = TIM_OCMode_PWM1;              // Set PWM1 Mode
  TIM_OCInitStruct.TIM_OutputState = TIM_OutputState_Enable;  // Enable OC
  TIM_OCInitStruct.TIM_Pulse = BLDC_PWM_MIN;                  // Set Pulse
  TIM_OCInitStruct.TIM_OCPolarity = TIM_OCPolarity_High;      // when Count < PWM_MOTOR_MIN => High
  TIM_OC1Init(TIM2, &TIM_OCInitStruct);                       // Init TIM2 OC1
  TIM_OC2Init(TIM2, &TIM_OCInitStruct);                       // Init TIM2 OC2
  TIM_OC3Init(TIM2, &TIM_OCInitStruct);                       // Init TIM2 OC3
  TIM_OC4Init(TIM2, &TIM_OCInitStruct);                       // Init TIM2 OC4
  TIM_OC1Init(TIM3, &TIM_OCInitStruct);                       // Init TIM3 OC1
  TIM_OC2Init(TIM3, &TIM_OCInitStruct);                       // Init TIM3 OC2
  TIM_OC3Init(TIM3, &TIM_OCInitStruct);                       // Init TIM3 OC3
  TIM_OC4Init(TIM3, &TIM_OCInitStruct);                       // Init TIM3 OC4
  TIM_OC3Init(TIM4, &TIM_OCInitStruct);                       // Init TIM4 OC3
  TIM_OC4Init(TIM4, &TIM_OCInitStruct);                       // Init TIM4 OC4
  TIM_OC1PreloadConfig(TIM2, TIM_OCPreload_Enable);           // Enable TIM2 OC1 Preload
  TIM_OC2PreloadConfig(TIM2, TIM_OCPreload_Enable);           // Enable TIM2 OC2 Preload
  TIM_OC3PreloadConfig(TIM2, TIM_OCPreload_Enable);           // Enable TIM2 OC3 Preload
  TIM_OC4PreloadConfig(TIM2, TIM_OCPreload_Enable);           // Enable TIM2 OC4 Preload
  TIM_OC1PreloadConfig(TIM3, TIM_OCPreload_Enable);           // Enable TIM3 OC1 Preload
  TIM_OC2PreloadConfig(TIM3, TIM_OCPreload_Enable);           // Enable TIM3 OC2 Preload
  TIM_OC3PreloadConfig(TIM3, TIM_OCPreload_Enable);           // Enable TIM3 OC3 Preload
  TIM_OC4PreloadConfig(TIM3, TIM_OCPreload_Enable);           // Enable TIM3 OC4 Preload
  TIM_OC3PreloadConfig(TIM4, TIM_OCPreload_Enable);           // Enable TIM4 OC3 Preload
  TIM_OC4PreloadConfig(TIM4, TIM_OCPreload_Enable);           // Enable TIM4 OC4 Preload

  /* Enable */
  TIM_ARRPreloadConfig(TIM2, ENABLE);                         // Enable TIM2 ARR Preload
  TIM_ARRPreloadConfig(TIM3, ENABLE);                         // Enable TIM3 ARR Preload
  TIM_ARRPreloadConfig(TIM4, ENABLE);                         // Enable TIM4 ARR Preload
  TIM_Cmd(TIM2, ENABLE);                                      // Start TIM2
  TIM_Cmd(TIM3, ENABLE);                                      // Start TIM3
  TIM_Cmd(TIM4, ENABLE);                                      // Start TIM4

  PWM1  = 0;
  PWM2  = 0;
  PWM3  = 0;
  PWM4  = 0;
  PWM9  = 0;
  PWM10 = 0;

  BLDC_M1 = BLDC_PWM_MIN;
  BLDC_M2 = BLDC_PWM_MIN;
  BLDC_M3 = BLDC_PWM_MIN;
  BLDC_M4 = BLDC_PWM_MIN;
}
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

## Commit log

2013-07-23 Revert "Update"
    This reverts commit 563859af58deafbb7c9819e5958a98518c912311.
    [QCopterFC.c, QCopterFC_ctrl.c, QCopterFC_ctrl.h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]
2013-07-25 PCB Update
    [QCopterFC.PrjPCB, QCopterFC_CAMSPI_Sch.SchDoc, QCopterFC_EXTERN_Sch.SchDoc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]
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2013-08-01 Update IMU PCB
    [IMU.PrjPCB, IMU_Pcb.PcbDoc, IMU_Sch.SchDoc]
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2013-09-14 Update QCopterFC v2.0
    [QCopterFC.PrjPCB, QCopterFC_CAMSPI_Sch.SchDoc, QCopterFC_EXTERN_Sch.SchDoc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]
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2013-10-17 Update QcopterFC_FlightControl 10/17
    + Read AK8975 Device ID
2013-10-21 Update TEST_QCopterFC_IMU 10/21
    Read 3-Axis Magnetometer
2013-11-01 Update QcopterFC_FlightControl 11/01
    Update I2C
2013-11-04 Update QcopterFC_FlightControl 11/04
    Update I2C Lib
2013-12-19 Update QCopterFC_FlightControl 12/20
    更新 StdPeriph_Lib v1.3
2013-12-19 Move to Google Drive 12/20
    移動 BOM 和 Config 至 Google Drive
2013-12-25 Update Readme 12/26
    增加 QFC TO QRC 的傳輸資料格式
2013-12-28 Update TEST_QCopterFC_LED 12/29
    更新 QCopterFC LED 範例的 StdPeriph_Lib
2013-12-28 Update TEST_QCopterFC_UART 12/29
    更新 QCopterFC UART 範例的 StdPeriph_Lib v1.3
2014-01-01 Update TEST_QCopterFC_SDIO 01/01
    ．更新 StdPeriph_Lib v1.3
    ．加入 Readme.md 檔案
2014-01-01 Update Readme.md 01/02
    修改 QCopterFC v2.2 預計改版內容
2014-01-01 Update Readme.md 01/02
    微調格式
2014-01-01 Update Readme.md 01/02
    微調改版內容
2014-01-04 Update QCopterFC_FlightControl 01/04
    更新飛控程式
    ．新增 QRC 和 QFC 之間的傳輸格式
    ．修改油門控制方式改為利用油門比例做控制
2014-01-05 Update QCopterFC_FlightControl 01/06
    ．微調油門控制問題
    ．加入 PID 平衡（尚未調整參數驗證）
2014-01-09 Update Readme.md 01/09
    修改 Module 及 PcbLib 連結
2014-01-14 Update Readme.md 01/14
    轉移至 QCopter
2014-01-16 Update TestLED 01/17
    微調文件放置
2014-01-17 Update TestLED 01/18
    修改 DEMO
2014-01-17 Update TestUART 01/18
    微調 UART RS232 傳輸函式
2014-01-17 Update TestFLASH 01/18
    更新測範例 StdLib v1.3
    加入 Readme.md
2014-01-20 Update Readme.md 01/20
    詳細授權部分
2014-01-20 Update License 01/20
    詳細授權內容
2014-01-20 Update Readme.md
    ．CC BY-SA 3.0 改為 CC BY-SA 3.0 TW
    ．調整 創用CC BY-SA logo
2014-01-20 Update Readme.md 01/20
    微調排版
2014-01-20 Change Directory 01/20
    Program 資料夾改名為 Software
2014-01-22 Update Readme.md 01/23
    改版 QCopterFC v2.2 中 ...
    ．重新設計 IMU 電路 ( MPU9250 & MS5611 )
    ．規劃元件位置、占用面積
2014-01-24 Update TestCamSPI 01/24
    更新 CamSPI 測試，並加入 QFC CamSPI Slave
2014-01-24 Update Readme.md 01/24
    更新 Test Readme.md 說明
2014-01-24 Update TestADC 01/24
    更新 TestADC 測試，並新增 TestADC Readme.md
2014-01-24 Update TestIMU 01/24
    更新測試程式，新增說明
2014-01-24 Update Readme.md 01/24
    更改名稱 & 加入 TestIMU 連結
2014-01-24 Update Readme.md
    更新 TestSDIO Readme.md 排版
2014-01-24 Update TestPWM 01/25
    更新 TestPWM 測試程式，加入說明文件
2014-01-24 Update Readme.md 01/25
    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
2014-01-24 Update Readme.md 01/25
    加入 TestPWM 程式連結
2014-01-25 Update TestNRF 01/26
    更新 TestNRF 測試程式，並新增說明文件
2014-01-25 Update Readme.md 01/26
    ．加入 TestNRF 程式連結
    ．微調圖片尺寸
2014-01-25 Update TestNRF Readme.md 01/26
    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
2014-01-25 Update FUTURE.md 01/26
    新增待完善功能
2014-01-25 Update Readme.md 01/26
    修正連結
2014-01-26 Update QCopterFC_FlightControl 01/27
    重新建立新版飛控程式
2014-01-26 Update QCopterFC_FlightControl Readme.md 01/27
    加入主要運作程式說明
2014-01-26 Update QCopterFC_FlightControl Readme.md 01/27
    修改錯字
2014-01-26 Update Readme.md 01/27
    修改預計改內容
2014-01-26 Update FUTURE.md 01/27
    新增可能改變計畫
2014-01-27 Update README 01/27
    修改 Related Documents 連結
2014-01-27 Update QCopterFC_FlightControl 01/28
    ．將 IMU 讀取部分整合至 Sensor_Read() 函數上
    ．調整氣壓計 MS5611 函數，去掉非必要資訊
2014-01-28 Update README 01/28
    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
2014-01-29 Update QCopterFC_FlightControl 01/29
    更先參數部分
    建立 PARAM 結構來集中重要參數
2014-01-31 Update FUTURE 01/31
    在"無線傳輸部分"
    加入"增加 RF 傳輸穩定度、傳輸速度"
2014-02-02 Update QCopterFC_FlightControl 02/02
    ．加入 QCopterFC_transport 檔案
    ．調整 RF 傳輸函式，並降低傳輸速率至 250Kb
2014-02-25 Update TEST_QCopterFC_PWM 02/25
    修正 TIM8 無法輸出 PWM 問題。
2014-02-25 Update README 02/25
    調整排版
2014-03-27 Update README 03/27
    預先將 v2.0 版本更新成 v2.2 版本，目前 v2.2 版本正在設計製作中。
2014-03-27 Update Hardware Pre-v2.2 03/27
    [QCopterFC.PrjPCB, QCopterFC_CAMSPI_Sch.SchDoc, QCopterFC_EXTERN_Sch.SchDoc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]
2014-04-10 Update Hardware Pre-v2.2 04/11
    更新 PCB 電路，並加入 Gerber File
    [QCopterFC.PrjPCB, QCopterFC_KEY_Sch.SchDoc, QCopterFC_MAIN_Sch.SchDoc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]
2014-04-11 Update README 04/11
    更新電路圖連結，並加入 pdf 版本電路圖，方便直接檢閱
2014-04-21 Update README 04/21
    ．調整 PCB 檔案，並加入實際送廠 Gerber
    ．修正電路圖
    [QCopterFC.PrjPCB, QCopterFC_IMU_Sch.SchDoc, QCopterFC_MAIN_Sch.SchDoc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]
2014-04-21 Update Schematic 04/21
    更新 Schematic View
    [QCopterFC_MAIN_Sch.SchDoc, QCopterFC__Sch.SchDoc]
2014-04-21 Update License 04/22
    完善 QCopter Flight Control v2.2 授權訊息
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2014-04-24 Update README 04/25
    修正圖片右上角電源輸入標示錯誤 ( 原 VIN, 誤標成 3V3 )
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2014-05-06 Update TEST_QCopterFC_TestFFCSPI-TFT2.2 05/06
    新增 FFCSPI 讀寫 TFT 2.2-inch 範例
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2014-06-10 Update Hardware v2.2
    v2.2 確定無誤版本
    [QCopterFC_EXT_Sch.SchDoc, QCopterFC_FFC_Sch.SchDoc, QCopterFC_IMU_Sch.SchDoc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]
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2014-07-07 Update TEST_QCopterFC_IAP-LED 07/08
    加入 IAP-LED 測試程式 ( TEST_QCopterFC_LED IAP 版本 )
2014-07-07 Update TEST_QCopterFC_IAP 07/08
    ．更新 FLASH EraseSector 函式，不須透過 GetSector 轉換
    ．增加 UART 與 Update 速度 ( 一次傳/寫 4K bytes )
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2014-07-08 Update README 07/09
    修正資料夾名稱
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2014-07-09 Update TEST_QCopterFC_UART 07/10
    更新 UART 測試程式，加入 UART RX
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2017-03-25 Add README 03/25
    [QCopterFC.PrjPCB, QCopterFC_EXT_Sch.SchDoc, QCopterFC_FFC_Sch.SchDoc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]
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2017-03-27 Add Hardware v1.0 03/27
    [QCopterFCs.PrjPCB, QCopterFCs_Pcb.PcbDoc, QCopterFCs_Sch.SchDoc]

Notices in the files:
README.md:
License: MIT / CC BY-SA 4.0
